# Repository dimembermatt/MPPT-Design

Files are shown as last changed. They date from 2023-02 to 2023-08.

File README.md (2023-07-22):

# :sunny: Sunscatter MPPT-Design - Gen 2 Maximum Power Point Tracker Board

Design and documentation of a custom MPPT for LHR Solar. Created in part with
Professor Alex Hanson's ECE 394J Power Electronics Class.

---

## Repository Structure

- **datasheets** - contains datasheets for major components of the Sunscatter.
- **docs** - contains documentation on how to build, test, and use the Sunscatter.
- **fw** - contains fw that is loaded onto the Sunscatter.
  - **tests** - test programs used to characterize and validate the Sunscatter.
  - **src** - main program used to run the Sunscatter.
  - **inc** - internally developed libraries specific for the Sunscatter.
  - **lib** - third party libraries used by the Sunscatter.
- **hw**
  - **footprints** - project specfic footprint association files for the Sunscatter.
  - **models** - 3d .step files for the PCB 3d viewer.
  - **symbols** - project specific symbol files for the Sunscatter.
  - **vX_Y_Z** - frozen versioning folder for PCB production files.
  - design files
- **sim** - contains a KiCAD project of the bare DC-DC converter of the MPPT, using SPICE parts for simulation.
- **sw** - contains relevant software for operating the automated design pipeline.
  - **design_files**
  - **design_procedures**

---

## Maintainers

The current maintainer of this project is Matthew Yu as of 07/17/2023. His email
is [matthewjkyu@gmail.com](matthewjkyu@gmail.com).

Contributors to the HW and FW encompass many dedicated students, including:

- Jacob Pustilnik
- Pranav Rama
- Sharon Chen

Special thanks to Professor Gary Hallock, who supervised the development and
design of this project.

---

## Versioning

This PCB is on unified version `0.2.0`. Every time the schematic and/or layout
is updated, this version number should go up. We use [semantic
versioning](https://semver.org/) to denote between versions. See the
[changelog](./docs/CHANGELOG.md) for more details.

---

## TODO

### Documentation

### HW

### FW

### SW

### Sim

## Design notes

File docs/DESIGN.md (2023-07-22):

# v0.1.0 DESIGN

TODO: update this consistent with all design versions.
---

## Table of Contents

- [v0.1.0 DESIGN](#v010-design)
  - [TODO: update this consistent with all design versions.](#todo-update-this-consistent-with-all-design-versions)
  - [Table of Contents](#table-of-contents)
  - [Introduction](#introduction)
  - [System Design Requirements](#system-design-requirements)
    - [Input](#input)
    - [Output](#output)
    - [User Specifications](#user-specifications)
  - [Hand Design](#hand-design)
    - [Switch Selection](#switch-selection)
    - [Input and Output Capacitor Selection](#input-and-output-capacitor-selection)
    - [Inductor Selection](#inductor-selection)
      - [Hand Designed Process](#hand-designed-process)
      - [Reverse Engineered Process](#reverse-engineered-process)
    - [Layout](#layout)
    - [Simulation Results](#simulation-results)
    - [Experimental Results](#experimental-results)
  - [Automated Design](#automated-design)
    - [Optimizer Design Output](#optimizer-design-output)
      - [Capacitor FOM](#capacitor-fom)
      - [Inductor Optimization](#inductor-optimization)
    - [Optimizer Simulation Output](#optimizer-simulation-output)
  - [Conclusion and Further Work](#conclusion-and-further-work)

---

## Introduction

This document outlines the design process and results of two comparable MPPT
designs; one that was developed by hand and validated experimentally; the other
generated by our optimization algorithm pipeline.

---

## System Design Requirements

---

### Input

We define the input of the MPPT to be a solar array, consisting of a large
number of photovoltaic cells strung in series with bypass diodes across each
cluster of cells. This solar array, in optimal conditions (STC = $25 \, C$,
$1000 \frac{W}{m^2}$), shall have the following characteristics.

| Property | Value  | Units |
|---|---|---|
| Cell Specific | | |
| $V_{OC}$ | 0.721  | V |
| $I_{SC}$ | 6.15 | A |
| $V_{MPP}$ | 0.621  | V |
| $I_{MPP}$ | 5.84 | A |
| $P_{MPP}$ | 3.63 | W |
| Array Specific | | |
| $N_{CELLS}$ | 111 | |
| $V_{OC}$ | 80.031 | V |
| $I_{SC}$ | 6.15 | A |
| $V_{MPP}$ | 68.931 | V |
| $I_{MPP}$ | 5.84 | A |
| $P_{MPP}$ | 402.56 | W |

A specification of the cell characteristics and the model output used for this
design is shown below.

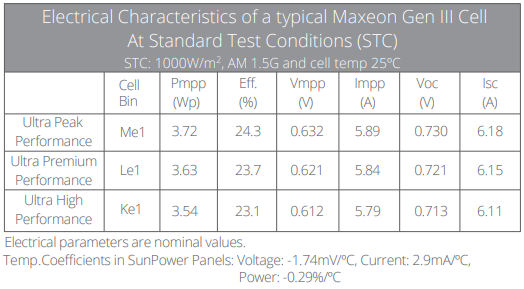
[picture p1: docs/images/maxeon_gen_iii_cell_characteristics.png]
Maxeon Gen III Cell Characteristics

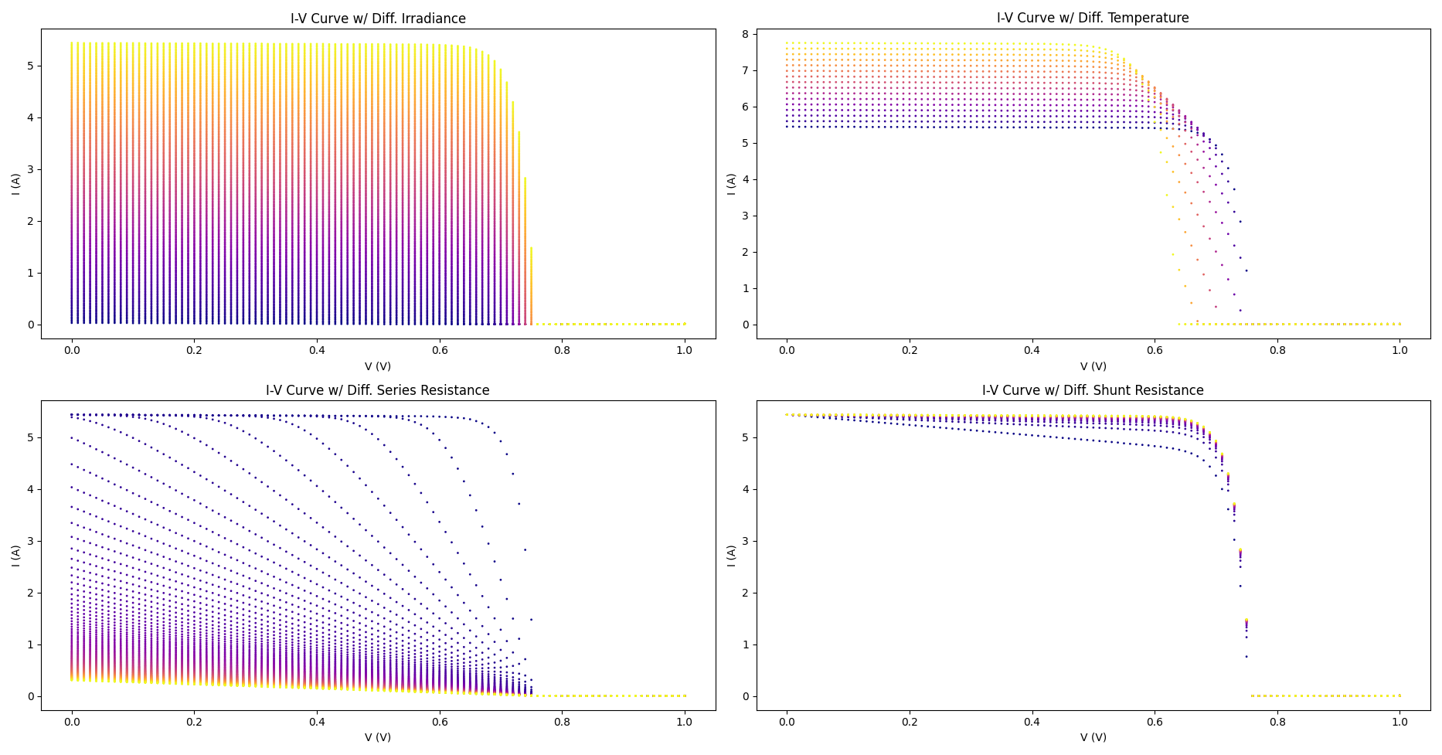
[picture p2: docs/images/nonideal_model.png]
Nonideal Cell Model


---

### Output

We define the output of the MPPT to be a LiMnNi battery pack, with a voltage
range of $V_{BATT} \in [80, 134.4] \, V$. We assume a maximum charging current
of $10 \, A$ at any charge voltage, for lack of a better model.

---

### User Specifications

Using the above input and output, we define the user specifications as follows:

```json
{
    "NAME": "Broad range MPPT",
    "AUTHORS": ["Matthew Yu", "Jacob Pustilnik"],
    "DESCRIPTION": "MPPT Boost Converter v0.1.0",
    "DATE_DESIGNED": "05/07/23",
    "DESIGN": {
        "input_source": {
            "source_model_type": "solar_cell",
            "cell_type": "Maxeon Gen III Bin Le1",
            "num_cells": 111,
            "r_sh": 40,
            "r_s": 0.0035,
            "inp_ripple (V)": 0.725,
            "user_v_range": [20.335, 74.481]
        },
        "output_sink": {
            "sink_model_type": "battery",
            "battery_type": "INR21700-M50LT",
            "num_cells": 32,
            "out_ripple (V)": 1.0,
            "user_v_range": [80, 130]
        },
        "safety_factor": 1.25
    }
}
```

We specify the shunt resistance and series resistance of the solar cell model as
based on empirical data with the I-V Curve Tracer testing setup.

We define the input voltage range to be $V_{ARR} \in [20.335, 74.481] \, V$
during the hand-design process to minimize switch stress and improve system
efficiency.

The input voltage peak-to-peak specification is slightly less than $1 \,\%$ of the
maximum input voltage ($74.481 \, V$).

The output voltage peak-to-peak specification is a conservative estimate of the
requirements of the LHR Solar BPS system. They did not give us a concrete number
(or any number, really), so we surmised that a $1 \, V_{pp}$ ripple should be
sufficient. This also means that for continuous transfer of energy in the
direction of the BPS, the output voltage of the system must be greater than the
voltage of the load plus the half of the ripple. A smaller ripple would allow us
to get closer to the load voltage and can marginally reduce switching stress.

The inductor current peak-to-peak specification is based on the typical $20\,\%$
current ripple ratio used in converters. It was increased to about $22.358\, \%$
due to the optimization process.

We use a safety factor of 1.25 to reduce system risk and improve operational
lifetime.

---

## Hand Design

The first version of this converter, version 0.1.0, was hand designed from
scratch. The following subsections discusses the methodology behind the design,
the expected and actual performance, and ultimately how it informs the automated
design process.

---

### Switch Selection

The main consideration for switch selection is the switching frequency relative
to the power loss; a better switch relative to another will have a higher
switching frequency for the same or less power consumption. Additionally, a
higher switching frequency has knock-on effects for passive selection; it
reduces the effective ripple experienced by the inductors and capacitors and
reduces their energy storage requirements.

One way to quantize switch performance is to use a Figure of Merit (FOM). The
established FOM for MOSFETs is $\tau = R_{DS,ON} * C_{OSS}$; a lower $\tau$
indicates a better switch.

We investigated a set of GaN switches, extracting $R_{DS,ON}$ values at $25 \,C$
and $125 \, C$ and $C_{OSS}$ values at $0 \, V$ and $150 \, V$. Taking the
average of these values, we established the FOM in $ps$.

GaN FETs

To determine the optimal switch, we took the top 12.5 percentile FOM and mapped
the $R_{DS,ON}$ vs $F_{SW,MAX}$ for a given power budget for various operating
points.

FOM Mapping

We see that the worst case plot is when the input voltage is minimized and the
output voltage is maximized. At an $R_{DS,ON}$ of about $19 \, m\Omega$. We
maximize the $F_{SW}$ at around $104 \, kHz$. It can be intuited that
an $R_{DS,ON}$ ratio to $C_{OSS}$ is slightly more important than the overall
FOM value.

As such, the ideal candidate for the design is the EPC2207, which has the
closest $R_{DS,ON}$ at the lowest FOM. This was not available at the time of
design, so the next closest candidate, the EPC2307 was chosen.

Rerunning the calculations of max lower bound $F_{SW}$ for a given power budget,
we achieved a switching frequency of $104 \, kHz$.

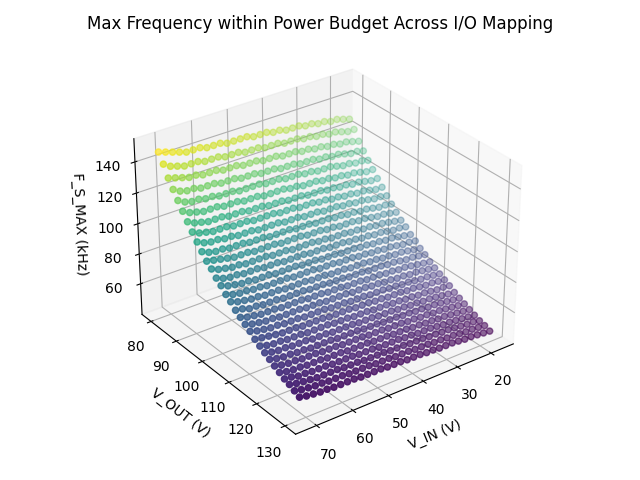
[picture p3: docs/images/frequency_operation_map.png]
$F_{SW}$ Mapping


---

### Input and Output Capacitor Selection

The input and output capacitor selection depends on several parameters:

- the required capacitance needed to reduce ripple to below the design
specification at the worst case operating point,
- the ripple current that needs to be supported by the set of capacitors,
- and the loss due to ESR and leakage current.

The first and second parameters are the constraining function of the capacitor
selection, while the third parameter is the optimization function of the
capacitor selection.

Given the switching frequency of the device, we simulated the minimum
capacitance (and inductance) required to hit the target ripple across the I/O
mapping of the device.

Passive Sizing Mapping

We noted a minimum required input capacitance of $5.5 \, \mu F$ and output capacitance
of $15.2 \, \mu F$ in order to meet or beat our ripple target across the I/O mapping
of the device.

From this, we selected capacitors for bulk capacitance and hf capacitance.
The input capacitor consisted of a single aluminum organic polymer electrolytic
capacitor A759KS156M2AAAE52, with a capacitance of $15 \, \mu F$. The output capacitors
consisted of two aluminum organic polymer electrolytic capacitors
A759MS186M2CAAE90, with a capacitance of $18 \, \mu F$. These bulk capacitances are well
beyond the required capacitance and thus we predict that the expected ripple
will be tighter than required.

We also selected a hf switching node MLCC capacitor to reduce switching noise,
the CGA9P3X7T2E225MA, with a capacitance of $2.2 \, \mu F$. At $125 \, V$ DC bias and
$125 \, C$, the capacitance derating goes down to slightly above $1 \, \mu F$. At
about $100 \, kHz$, the ESR is about $5.5 \, m\Omega$.

---

### Inductor Selection

The inductor selection consists of two components; the inductor core geometry,
and the inductor core material. An ideal inductor is one that minimizes volume
and wire length while keeping losses low.

The minimum inductance calculated by the procedure above was $109.2 \, \mu H$.

It must be noted here that the hand-designed process for calculating the
inductance neglected core gap, which caused issues during the experimental
testing. Below we will present the results of the flawed calculation versus the
reverse engineered variant using the automated design system.

---

#### Hand Designed Process

With a target $110 \, \mu H$ inductance, the hand-designed process generated a
design using the EPCOS/TDK PQ26/25, 3C97 core, the B65877A0000R097. It required
35 turns with a wire gauge of 21 AWG.

This results in a estimated conduction loss of $4.5 \, W$ and core loss of
$0.2 \, W$.

---

#### Reverse Engineered Process

Using the same core, the algorithm determined that the inductor requires 31
turns of 19 AWG wire with a core gap of $1.0 \, mm$ per side of the core.

This results in an estimated conduction loss of $0.3 \, W$ and a core loss of
$0.03 \, W$.

As can be seen, the reverse engineered process results in a much lower
conduction and core loss. Part of the changes between the two designs is that it
was determined experimentally that the 0.3 winding factor used for calculating
the number of turns that can fit around the core was an overly-conservative
estimate, this has been increased to 0.5. In tern, this allows for fitting a
thicker gauge wire which can significantly reduce conduction loss, which appears
to be the main mode of inductor loss during experimental testing.

---

### Layout

This layout section discusses component placement in brief; it does not discuss
in detail all PCB design decisions. Matthew could give an hour lecture if you
ask him to :).

Not discussed in document in detail is the gate driver and PWM generator; the
TI LMG1210RVRR gate driver was chosen for our particular GaN FETs, and the
STM32L432KC is a $80 \, MHz$ microcontroller with PWM outputs. The MCU is paired
with two voltage and current sensors at the ends of the power path for
measurement and closed loop control.

The digital and analog control and measurement circuitry is isolated on the
"top" half of the board layout; this is to prevent or reduce EMI from the
switching node and high current fluctuations.

The "bottom" half of the board layout is the power path; this is the DC-DC
converter and contains the capacitors, inductor, and switches. Components are
arranged relatively linearly to reduce the loop and shape complexity; the bulk
output capacitors can be slightly away from the switching loop but the HF
capacitor must be as close to the switches as possible. Likewise, the inductor
end must also be relatively close to the switches.

In our configuration, we put the switches side by side with the HF MLCC
capacitor directly underneath; this gives a very tight loop.

We also placed thermal jumpers between planes to help distribute heat. This is
accompanied by thermal and EMI stiching vias scattered across the board.

Layout
Assembly

---

### Simulation Results

The following graphs are generated from the automated design system with the
chosen devices provided as parameters.

Source Model

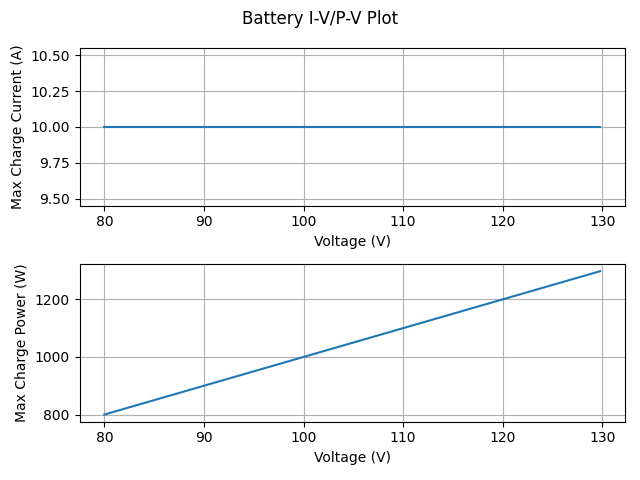
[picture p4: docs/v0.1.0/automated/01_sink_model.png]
Sink Model


Duty Cycle Map

Current Transfer Map

Power Transfer Map

Switch Losses Map

Switch Thermal Sizing

Switch Deadtime Sizing

Passive Ripple Map

Passive Losses Map

Efficiency Map

We note that the total power loss derived from the hand-picked design is
$7.63 \, W$, at the highest switching stress operating point: min input voltage,
max output voltage. This results in a minimum transfer efficiency of $93.92 \, \%$.

At this operating point the switch conduction loss and switching loss peaks,
contributing to about $3.60 \, W$ of loss each, with the inductor and output
capacitor providing the majority of the rest (generally through output capacitor
leakage loss and inductor conduction loss).

We also note that minimum required area needed to maintain both switches below
the maximum rated temperature time the 1 / safety factor starting from $60 \, C$ is
$70.893 \, cm^2$. The layout design has a total surface area of $110 \, cm^2$,
which is should be sufficient for cooling without an external heatsink.

---

### Experimental Results

Note for the purposes of the experimental testing, we ran the device at
$100 \, kHz$.

We also used an inductor wound at $155 \, \mu H$, with about 30 turns of AWG 21
wires, and a gap on each side of the core of roughly $0.318 \, mm$.

We obtained the following experimental results:

| Vin (V) | Vout (V) | Pout (W) | Eff (%) | Pdensity (W/cm3) | Vin, p-p (V) | Vout, p-p (V) | Il, p-p (A) |
|---|---|---|---|---|---|---|---|
| 67.524 (69) | 102.02 (105) | 380.87 (400) |  98.972 | 1.979 | 0.234 | 0.309 | 1.820 |
| Broad range tests | | | | | | | |
| 18.752 | 73.242 | 83.154 |  97.349 | 0.432 | 0.226 | 0.365 | 1.159 |
| 18.825 | 96.73 | 84.416 |  97.032 | 0.439 | 0.249 | 0.402 | 1.263 |
| 18.823 | 119.35 | 83.889 |  96.531 | 0.436 | 0.330 | 0.510 | 1.440 |
| 38.805 | 76.688 | 181.72 |  98.616 | 0.944 | 0.270 | 0.356 | 1.520 |
| 38.782 | 100.8 | 182.74 |  98.348 | 0.949 | 0.295 | 0.412 | 1.959 |
| 38.78 | 124.54 | 182.34 |  98.083 | 0.947 | 0.336 | 0.489 | 2.199 |
| 58.798 | 77.774 | 279.2 |  99.103 | 1.450 | 0.249 | 0.348 | 1.280 |
| 58.76 | 102.01 | 281.43 |  98.904 | 1.462 | 0.299 | 0.411 | 2.000 |
| 58.741 | 126.28 | 282.55 |  98.671 | 1.468 | 0.346 | 0.495 | 2.480 |
| 67.592 | 77.744 | 371.13 |  99.146 | 1.928 | 0.149 | 0.278 | 0.840 |
| 67.524 | 102.02 | 380.87 |  98.972 | 1.979 | 0.234 | 0.309 | 1.820 |
| 67.471 | 126.19 | 375.78 |  98.782 | 1.952 | 0.265 | 0.325 | 2.540 |
| 74.612 | 79.447 | 97.746 |  99.071 | 0.508 | 0.217 | 0.428 | 0.580 |
| 74.609 | 104.35 | 98.194 |  98.484 | 0.510 | 0.226 | 0.419 | 1.640 |
| 74.606 | 129.25 | 98.805 |  97.806 | 0.513 | 0.273 | 0.457 | 2.359 |

We note that the switching noise was minimal, indicating that the switching node
layout was optimized well enough to not severely impact the design results.

We measured a worst I/O mapping efficiency ($18.8 \, V$ to $119.3 \, V$) of
$96.5 \, \%$, exceeding our expected lower bound. We measured a best I/O mapping
efficiency ($67.6 \, V$ to $77.7 \, V$) of $99.1 \, \%$, within measurement error
to meet our upper bound.

We do not meet our simulated ripple results, potentially due the following
factors, but still comfortably beat our ripple specifications by up to 50%.

- measurement error (using oscilloscope)
- switching noise
- change in inductor design

We observe that the experimental data power loss map shows deviations from
simulation; if we observe the trend of loss increase across each axis, the
underlying switching and conduction loss agree. In between however, some
datapoints exceed expectations and have larger losses than can be explained by
simulations (although some may be attributable to inductor loss at the input
MPP).

Power Loss Map

Efficiency Map

Thermal wise, the losses were expected to be in two main components: the
switches and inductor. According to the thermal images, this shows up as
expected. The maximum recorded temperature of the switch devices was $60 \, C$,
from am ambient of about $20 \, C$, the 40 degree temperature increase is in
line with the anticipated loss at that particular operating point (~$3.6 \, W$).

Thermal Images

---

## Automated Design

Optimizer Block Diagram

An automated design optimizer algorithm was developed to speed up and improve
the design process outlined by the hand designed procedures.

A design specification file and a list of design components are provided, in
which the optimizer chooses the optimal parts and calculates the operating
parameters that maximizes system efficiency.

Optimizer Parameters and Constraints

The optimizer controls two parameters: the power budget allocated to each switch
and the inductor current ripple ratio. The user maintains constraints, including
the input voltage and output voltage range, or the safety factor of the design.

Optimizer Algorithm

As outlined in the optimizer algorithm, every design iteration starts with a
selection on the switch power budget and the inductor current ripple ratio. The
algorithm first determines the switch and the switching frequency before
selecting for an optimal set of capacitors and then the inductor configuration.
Finally, the overall worst case power loss is determined before repeating the
loop.

After many iterations, the optimizer settles on the parameters that lead to the
highest efficiency design. The output of these parameters results in the
selection of design components for use.

The automated design was ran on the same specification file and user constraints
as defined in the hand-designed section.

---

### Optimizer Design Output

It was evaluated that the optimal parameter values that led to the ideal design
was an $R_{L}$ of 0.119 and a $P_{SW\_BUD}$ of 2.13 W.

The switches chosen were the EPC2207 (now in stock), which had an optimal
frequency of $95 \, kHz$; this led to the following passive requirements:

- Input capacitance greater than $2.67 \, \mu F$
- Output capacitance greater than $16.16 \, \mu F$
- Inductance greater than $280.51 \, \mu H$.

---

#### Capacitor FOM

A custom FOM was developed for selecting optimal capacitors for the design. We
remind the reader of the parameters defined earlier in the hand-design section
for choosing capacitors:

> - the required capacitance needed to reduce ripple to below the design
>   specification at the worst case operating point,
> - the ripple current that needs to be supported by the set of capacitors,
> - and the loss due to ESR and leakage current.
>
> The first and second parameters are the constraining function of the capacitor
> selection, while the third parameter is the optimization function of the
> capacitor selection.

Ideally, we want to choose as few capacitors as possible to meet the first two
parameters, but also minimize the third parameter. As this is a multi-objective
optimization problem, the brute force method would be to form the power set of
all candidate capacitors, filter the sets that do not meet the constraints, and
choose the smallest and most optimal set.

However, we propose the following FOM equation to speed up the process:

$$
FOM = \frac{V_{D} * C * I_{RIPPLE}}{ESR * I_{LEAKAGE} * COST}
$$

As can be seen, this formula rewards higher constraints while punishing
undesirable aspects that affect power (and cost).

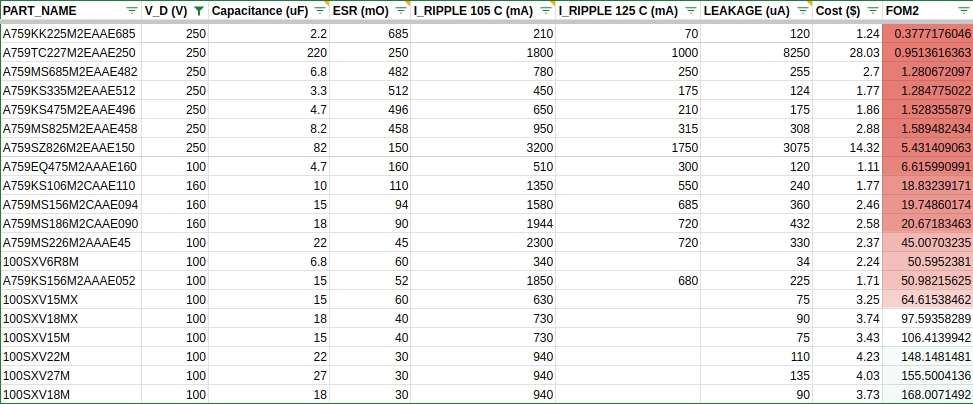
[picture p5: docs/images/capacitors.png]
Capacitors


A subset of capacitors with the FOM added is shown. We can see that the best FOM
capacitors tended to have reasonable capacitance, ripple, and cost, but low ESR,
and leakage.

Ultimately this worked well for this design, with the optimizer choosing the
HZA336M080G24T-F $33 \, \mu F$ aluminium electrolytic capacitor for the input
and the A759MS186M2CAAE090 $18 \, \mu F$ aluminum organic polymer electrolytic
capacitor for the output.

---

#### Inductor Optimization

The optimizer selected a slightly different core than the hand-design, a
PQ26/25-3C96 with 53 turns of 21 AWG wire. A core gap of 1.4 mm is suggested.

Inductor selection was performed with extra component listings for the core
shape and material: the material in particular provided constants calculated by
FerroxCube to calculate the core loss with Steinmetz' equation. This meant that
there was no need to manually infer the $P_{V}$ from the manufacturer datasheet
for our particular frequency, core shape, and temperature.

The optimization procedure only optimizes for loss, however; other parameters of
interest, like cost and core size are neglected in favor of the design with the
least conduction and core loss.

---

### Optimizer Simulation Output

The following graphs are generated from the automated design system with the
chosen devices provided as parameters.

Source Model

Sink Model

Duty Cycle Map

Current Transfer Map

Power Transfer Map

Switch Losses Map

Switch Thermal Sizing

Switch Deadtime Sizing

Passive Ripple Map

Passive Losses Map

Efficiency Map

We note that the total power loss derived from the automated design is
$5.04 \, W$, at the highest switching stress operating point: min input voltage,
max output voltage. This results in a minimum transfer efficiency of $96.0 \, \%$.

At this operating point the switch conduction loss and switching loss peaks,
contributing to about $2.12 \, W$ of loss each, with the inductor conduction
loss providing the rest.

We also note that minimum required area needed to maintain both switches below
the maximum rated temperature time the 1 / safety factor starting from $60 \, C$ is
$35.546 \, cm^2$, a 2x improvement. This allows us to shrink the required
exposed thermal area by a significant margin, and should enable us to remove the
existing thermal jumpers.

Also notably improved is the dead time, with the majority of the design only
needing at most $12 ns$ of deadtime.

We see that this automated design beats the reverse engineered hand-designed
version by at least $2 \, \%$. The upper bound efficiency also improves
marginally. At the same time, our expected number of capacitors decreases, our
required thermal area shrinks, and thus we can remove extraneous components like
heat sinks, and thermal jumpers.

Judging by our empirical losses, it would be very positive if we can exceed our
lower bound efficiency estimate again.

---

## Conclusion and Further Work

In conclusion, the overall system design is a good starting point towards
modeling DC-DC converters with only a few known parameters. A hand-designed
system is compared against a fully automated result, and the initial efficiency
results, both simulated and emperical, show high marks. The automated design
appears to improve upon the hand-designed converter by at least $2 \, \%$ in the
worst operating regime, which is promising.

In this report, we do not discuss the open and closed loop stability of the
design. However, we have validated that the system is indeed open and closed
loop stable. Further work in this project will involve the small signal and
large signal stability analysis of the system to characterize the stability of
the system before comparing it against empirical stability.

In addition to this analysis, further effort should be performed to gather higher
resolution steady state efficiency. More experimental data points can help
inform the accuracy of the model and where the design process can be improved.

Further research into choosing an appropriate FOM should be performed.
While the proposed FOM works well for this design, it is likely not optimal in
all cases: a brute force solution should be determined as the golden reference,
and a PCA or curve fitting technique should be performed on the available
capacitor parameters to determine weightings for the values that match the golden
reference.

Finally, work into automating the decision of choosing HF capacitors should be
performed. This is slightly more difficult for MLCCs due to the data-intensive
work of gathering frequency vs impedance CSVs (and so forth) from manufacturers
that provide them, such as KEMET and TDK. However, their data can improve the
optimization process and provide useful insight into stability analysis due to
their effects on the design poles and holes.

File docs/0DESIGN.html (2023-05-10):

# v0.1.0 DESIGN

## Table of Contents

- v0.1.0 DESIGN
  - Table of Contents
  - Introduction
  - System Design Requirements
    - Input
    - Output
    - User Specifications
  - Hand Design
    - Switch Selection
    - Input and Output Capacitor Selection
    - Inductor Selection
      - Hand Designed Process
      - Reverse Engineered Process
    - Layout
    - Simulation Results
    - Experimental Results
  - Automated Design
    - Optimizer Design Output
      - Capacitor FOM
      - Inductor Optimization
    - Optimizer Simulation Output
  - Conclusion and Further Work

## Introduction

This document outlines the design process and results of two comparable MPPT designs; one that was developed by hand and validated experimentally; the other generated by our optimization algorithm pipeline.

## System Design Requirements

### Input

We define the input of the MPPT to be a solar array, consisting of a large number of photovoltaic cells strung in series with bypass diodes across each cluster of cells. This solar array, in optimal conditions (STC = 25 \, C, 1000 \frac{W}{m^2}), shall have the following characteristics.

Property | Value | Units
Cell Specific
V_{OC} | 0.721 | V
I_{SC} | 6.15 | A
V_{MPP} | 0.621 | V
I_{MPP} | 5.84 | A
P_{MPP} | 3.63 | W
Array Specific
N_{CELLS} | 111
V_{OC} | 80.031 | V
I_{SC} | 6.15 | A
V_{MPP} | 68.931 | V
I_{MPP} | 5.84 | A
P_{MPP} | 402.56 | W

A specification of the cell characteristics and the model output used for this design is shown below.

Maxeon Gen III Cell Characteristics Nonideal Cell Model

### Output

We define the output of the MPPT to be a LiMnNi battery pack, with a voltage range of V_{BATT} \in [80, 134.4] \, V. We assume a maximum charging current of 10 \, A at any charge voltage, for lack of a better model.

### User Specifications

Using the above input and output, we define the user specifications as follows:

{
    "NAME": "Broad range MPPT",
    "AUTHORS": ["Matthew Yu", "Jacob Pustilnik"],
    "DESCRIPTION": "MPPT Boost Converter v0.1.0",
    "DATE_DESIGNED": "05/07/23",
    "DESIGN": {
        "input_source": {
            "source_model_type": "solar_cell",
            "cell_type": "Maxeon Gen III Bin Le1",
            "num_cells": 111,
            "r_sh": 40,
            "r_s": 0.0035,
            "inp_ripple (V)": 0.725,
            "user_v_range": [20.335, 74.481]
        },
        "output_sink": {
            "sink_model_type": "battery",
            "battery_type": "INR21700-M50LT",
            "num_cells": 32,
            "out_ripple (V)": 1.0,
            "user_v_range": [80, 130]
        },
        "safety_factor": 1.25
    }
}

We specify the shunt resistance and series resistance of the solar cell model as based on empirical data with the I-V Curve Tracer testing setup.

We define the input voltage range to be V_{ARR} \in [20.335, 74.481] \, V during the hand-design process to minimize switch stress and improve system efficiency.

The input voltage peak-to-peak specification is slightly less than 1 \,\% of the maximum input voltage (74.481 \, V).

The output voltage peak-to-peak specification is a conservative estimate of the requirements of the LHR Solar BPS system. They did not give us a concrete number (or any number, really), so we surmised that a 1 \, V_{pp} ripple should be sufficient. This also means that for continuous transfer of energy in the direction of the BPS, the output voltage of the system must be greater than the voltage of the load plus the half of the ripple. A smaller ripple would allow us to get closer to the load voltage and can marginally reduce switching stress.

The inductor current peak-to-peak specification is based on the typical 20\,\% current ripple ratio used in converters. It was increased to about 22.358\, \% due to the optimization process.

We use a safety factor of 1.25 to reduce system risk and improve operational lifetime.

## Hand Design

The first version of this converter, version 0.1.0, was hand designed from scratch. The following subsections discusses the methodology behind the design, the expected and actual performance, and ultimately how it informs the automated design process.

### Switch Selection

The main consideration for switch selection is the switching frequency relative to the power loss; a better switch relative to another will have a higher switching frequency for the same or less power consumption. Additionally, a higher switching frequency has knock-on effects for passive selection; it reduces the effective ripple experienced by the inductors and capacitors and reduces their energy storage requirements.

One way to quantize switch performance is to use a Figure of Merit (FOM). The established FOM for MOSFETs is \tau = R_{DS,ON} * C_{OSS}; a lower \tau indicates a better switch.

We investigated a set of GaN switches, extracting R_{DS,ON} values at 25 \,C and 125 \, C and C_{OSS} values at 0 \, V and 150 \, V. Taking the average of these values, we established the FOM in ps.

GaN FETs

To determine the optimal switch, we took the top 12.5 percentile FOM and mapped the R_{DS,ON} vs F_{SW,MAX} for a given power budget for various operating points.

FOM Mapping

We see that the worst case plot is when the input voltage is minimized and the output voltage is maximized. At an R_{DS,ON} of about 19 \, m\Omega. We maximize the F_{SW} at around 104 \, kHz. It can be intuited that an R_{DS,ON} ratio to C_{OSS} is slightly more important than the overall FOM value.

As such, the ideal candidate for the design is the EPC2207, which has the closest R_{DS,ON} at the lowest FOM. This was not available at the time of design, so the next closest candidate, the EPC2307 was chosen.

Rerunning the calculations of max lower bound F_{SW} for a given power budget, we achieved a switching frequency of 104 \, kHz.

Mapping

### Input and Output Capacitor Selection

The input and output capacitor selection depends on several parameters:

- the required capacitance needed to reduce ripple to below the design specification at the worst case operating point,
- the ripple current that needs to be supported by the set of capacitors,
- and the loss due to ESR and leakage current.

The first and second parameters are the constraining function of the capacitor selection, while the third parameter is the optimization function of the capacitor selection.

Given the switching frequency of the device, we simulated the minimum capacitance (and inductance) required to hit the target ripple across the I/O mapping of the device.

Passive Sizing Mapping

We noted a minimum required input capacitance of 5.5 \, \mu F and output capacitance of 15.2 \, \mu F in order to meet or beat our ripple target across the I/O mapping of the device.

From this, we selected capacitors for bulk capacitance and hf capacitance. The input capacitor consisted of a single aluminum organic polymer electrolytic capacitor A759KS156M2AAAE52, with a capacitance of 15 \, \mu F. The output capacitors consisted of two aluminum organic polymer electrolytic capacitors A759MS186M2CAAE90, with a capacitance of 18 \, \mu F. These bulk capacitances are well beyond the required capacitance and thus we predict that the expected ripple will be tighter than required.

We also selected a hf switching node MLCC capacitor to reduce switching noise, the CGA9P3X7T2E225MA, with a capacitance of 2.2 \, \mu F. At 125 \, V DC bias and 125 \, C, the capacitance derating goes down to slightly above 1 \, \mu F. At about 100 \, kHz, the ESR is about 5.5 \, m\Omega.

### Inductor Selection

The inductor selection consists of two components; the inductor core geometry, and the inductor core material. An ideal inductor is one that minimizes volume and wire length while keeping losses low.

The minimum inductance calculated by the procedure above was 109.2 \, \mu H.

It must be noted here that the hand-designed process for calculating the inductance neglected core gap, which caused issues during the experimental testing. Below we will present the results of the flawed calculation versus the reverse engineered variant using the automated design system.

#### Hand Designed Process

With a target 110 \, \mu H inductance, the hand-designed process generated a design using the EPCOS/TDK PQ26/25, 3C97 core, the B65877A0000R097. It required 35 turns with a wire gauge of 21 AWG.

This results in a estimated conduction loss of 4.5 \, W and core loss of 0.2 \, W.

#### Reverse Engineered Process

Using the same core, the algorithm determined that the inductor requires 31 turns of 19 AWG wire with a core gap of 1.0 \, mm per side of the core.

This results in an estimated conduction loss of 0.3 \, W and a core loss of 0.03 \, W.

As can be seen, the reverse engineered process results in a much lower conduction and core loss. Part of the changes between the two designs is that it was determined experimentally that the 0.3 winding factor used for calculating the number of turns that can fit around the core was an overly-conservative estimate, this has been increased to 0.5. In tern, this allows for fitting a thicker gauge wire which can significantly reduce conduction loss, which appears to be the main mode of inductor loss during experimental testing.

### Layout

This layout section discusses component placement in brief; it does not discuss in detail all PCB design decisions. Matthew could give an hour lecture if you ask him to :).

Not discussed in document in detail is the gate driver and PWM generator; the TI LMG1210RVRR gate driver was chosen for our particular GaN FETs, and the STM32L432KC is a 80 \, MHz microcontroller with PWM outputs. The MCU is paired with two voltage and current sensors at the ends of the power path for measurement and closed loop control.

The digital and analog control and measurement circuitry is isolated on the "top" half of the board layout; this is to prevent or reduce EMI from the switching node and high current fluctuations.

The "bottom" half of the board layout is the power path; this is the DC-DC converter and contains the capacitors, inductor, and switches. Components are arranged relatively linearly to reduce the loop and shape complexity; the bulk output capacitors can be slightly away from the switching loop but the HF capacitor must be as close to the switches as possible. Likewise, the inductor end must also be relatively close to the switches.

In our configuration, we put the switches side by side with the HF MLCC capacitor directly underneath; this gives a very tight loop.

We also placed thermal jumpers between planes to help distribute heat. This is accompanied by thermal and EMI stiching vias scattered across the board.

Layout Assembly

### Simulation Results

The following graphs are generated from the automated design system with the chosen devices provided as parameters.

Source Model

Sink Model

Duty Cycle Map

Current Transfer Map

Power Transfer Map

Switch Losses Map

Switch Thermal Sizing

Switch Deadtime Sizing

Passive Ripple Map

Passive Losses Map

Efficiency Map

We note that the total power loss derived from the hand-picked design is 7.63 \, W, at the highest switching stress operating point: min input voltage, max output voltage. This results in a minimum transfer efficiency of 93.92 \, \%.

At this operating point the switch conduction loss and switching loss peaks, contributing to about 3.60 \, W of loss each, with the inductor and output capacitor providing the majority of the rest (generally through output capacitor leakage loss and inductor conduction loss).

We also note that minimum required area needed to maintain both switches below the maximum rated temperature time the 1 / safety factor starting from 60 \, C is 70.893 \, cm^2. The layout design has a total surface area of 110 \, cm^2, which is should be sufficient for cooling without an external heatsink.

### Experimental Results

Note for the purposes of the experimental testing, we ran the device at 100 \, kHz.

We also used an inductor wound at 155 \, \mu H, with about 30 turns of AWG 21 wires, and a gap on each side of the core of roughly 0.318 \, mm.

We obtained the following experimental results:

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

We note that the switching noise was minimal, indicating that the switching node layout was optimized well enough to not severely impact the design results.

We measured a worst I/O mapping efficiency (18.8 \, V to 119.3 \, V) of 96.5 \, \%, exceeding our expected lower bound. We measured a best I/O mapping efficiency (67.6 \, V to 77.7 \, V) of 99.1 \, \%, within measurement error to meet our upper bound.

We do not meet our simulated ripple results, potentially due the following factors, but still comfortably beat our ripple specifications by up to 50%.

- measurement error (using oscilloscope)
- switching noise
- change in inductor design

We observe that the experimental data power loss map shows deviations from simulation; if we observe the trend of loss increase across each axis, the underlying switching and conduction loss agree. In between however, some datapoints exceed expectations and have larger losses than can be explained by simulations (although some may be attributable to inductor loss at the input MPP).

Power Loss Map

Efficiency Map

Thermal wise, the losses were expected to be in two main components: the switches and inductor. According to the thermal images, this shows up as expected. The maximum recorded temperature of the switch devices was 60 \, C, from am ambient of about 20 \, C, the 40 degree temperature increase is in line with the anticipated loss at that particular operating point (~3.6 \, W).

Thermal Images

## Automated Design

Optimizer Block Diagram

An automated design optimizer algorithm was developed to speed up and improve the design process outlined by the hand designed procedures.

A design specification file and a list of design components are provided, in which the optimizer chooses the optimal parts and calculates the operating parameters that maximizes system efficiency.

Optimizer Parameters and Constraints

The optimizer controls two parameters: the power budget allocated to each switch and the inductor current ripple ratio. The user maintains constraints, including the input voltage and output voltage range, or the safety factor of the design.

Optimizer Algorithm

As outlined in the optimizer algorithm, every design iteration starts with a selection on the switch power budget and the inductor current ripple ratio. The algorithm first determines the switch and the switching frequency before selecting for an optimal set of capacitors and then the inductor configuration. Finally, the overall worst case power loss is determined before repeating the loop.

After many iterations, the optimizer settles on the parameters that lead to the highest efficiency design. The output of these parameters results in the selection of design components for use.

The automated design was ran on the same specification file and user constraints as defined in the hand-designed section.

### Optimizer Design Output

It was evaluated that the optimal parameter values that led to the ideal design was an R_{L} of 0.119 and a P_{SW\_BUD} of 2.13 W.

The switches chosen were the EPC2207 (now in stock), which had an optimal frequency of 95 \, kHz; this led to the following passive requirements:

- Input capacitance greater than 2.67 \, \mu F
- Output capacitance greater than 16.16 \, \mu F
- Inductance greater than 280.51 \, \mu H.

#### Capacitor FOM

A custom FOM was developed for selecting optimal capacitors for the design. We remind the reader of the parameters defined earlier in the hand-design section for choosing capacitors:

- the required capacitance needed to reduce ripple to below the design specification at the worst case operating point,
- the ripple current that needs to be supported by the set of capacitors,
- and the loss due to ESR and leakage current.

The first and second parameters are the constraining function of the capacitor selection, while the third parameter is the optimization function of the capacitor selection.

Ideally, we want to choose as few capacitors as possible to meet the first two parameters, but also minimize the third parameter. As this is a multi-objective optimization problem, the brute force method would be to form the power set of all candidate capacitors, filter the sets that do not meet the constraints, and choose the smallest and most optimal set.

However, we propose the following FOM equation to speed up the process:

FOM = \frac{V_{D} * C * I_{RIPPLE}}{ESR * I_{LEAKAGE} * COST}

As can be seen, this formula rewards higher constraints while punishing undesirable aspects that affect power (and cost).

Capacitors

A subset of capacitors with the FOM added is shown. We can see that the best FOM capacitors tended to have reasonable capacitance, ripple, and cost, but low ESR, and leakage.

Ultimately this worked well for this design, with the optimizer choosing the HZA336M080G24T-F 33 \, \mu F aluminium electrolytic capacitor for the input and the A759MS186M2CAAE090 18 \, \mu F aluminum organic polymer electrolytic capacitor for the output.

#### Inductor Optimization

The optimizer selected a slightly different core than the hand-design, a PQ26/25-3C96 with 53 turns of 21 AWG wire. A core gap of 1.4 mm is suggested.

Inductor selection was performed with extra component listings for the core shape and material: the material in particular provided constants calculated by FerroxCube to calculate the core loss with Steinmetz' equation. This meant that there was no need to manually infer the P_{V} from the manufacturer datasheet for our particular frequency, core shape, and temperature.

The optimization procedure only optimizes for loss, however; other parameters of interest, like cost and core size are neglected in favor of the design with the least conduction and core loss.

### Optimizer Simulation Output

The following graphs are generated from the automated design system with the chosen devices provided as parameters.

Source Model

Sink Model

Duty Cycle Map

Current Transfer Map

Power Transfer Map

Switch Losses Map

Switch Thermal Sizing

Switch Deadtime Sizing

Passive Ripple Map

Passive Losses Map

Efficiency Map

We note that the total power loss derived from the automated design is 5.04 \, W, at the highest switching stress operating point: min input voltage, max output voltage. This results in a minimum transfer efficiency of 96.0 \, \%.

At this operating point the switch conduction loss and switching loss peaks, contributing to about 2.12 \, W of loss each, with the inductor conduction loss providing the rest.

We also note that minimum required area needed to maintain both switches below the maximum rated temperature time the 1 / safety factor starting from 60 \, C is 35.546 \, cm^2, a 2x improvement. This allows us to shrink the required exposed thermal area by a significant margin, and should enable us to remove the existing thermal jumpers.

Also notably improved is the dead time, with the majority of the design only needing at most 12 ns of deadtime.

We see that this automated design beats the reverse engineered hand-designed version by at least 2 \, \%. The upper bound efficiency also improves marginally. At the same time, our expected number of capacitors decreases, our required thermal area shrinks, and thus we can remove extraneous components like heat sinks, and thermal jumpers.

Judging by our empirical losses, it would be very positive if we can exceed our lower bound efficiency estimate again.

## Conclusion and Further Work

In conclusion, the overall system design is a good starting point towards modeling DC-DC converters with only a few known parameters. A hand-designed system is compared against a fully automated result, and the initial efficiency results, both simulated and emperical, show high marks. The automated design appears to improve upon the hand-designed converter by at least 2 \, \% in the worst operating regime, which is promising.

In this report, we do not discuss the open and closed loop stability of the design. However, we have validated that the system is indeed open and closed loop stable. Further work in this project will involve the small signal and large signal stability analysis of the system to characterize the stability of the system before comparing it against empirical stability.

In addition to this analysis, further effort should be performed to gather higher resolution steady state efficiency. More experimental data points can help inform the accuracy of the model and where the design process can be improved.

Further research into choosing an appropriate FOM should be performed. While the proposed FOM works well for this design, it is likely not optimal in all cases: a brute force solution should be determined as the golden reference, and a PCA or curve fitting technique should be performed on the available capacitor parameters to determine weightings for the values that match the golden reference.

Finally, work into automating the decision of choosing HF capacitors should be performed. This is slightly more difficult for MLCCs due to the data-intensive work of gathering frequency vs impedance CSVs (and so forth) from manufacturers that provide them, such as KEMET and TDK. However, their data can improve the optimization process and provide useful insight into stability analysis due to their effects on the design poles and holes.

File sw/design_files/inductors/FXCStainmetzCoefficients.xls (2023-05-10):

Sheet: Loss Coefficients
 |  |  |  |  |  |  |  |  |  | Freq |  |  | 200000 | Hz | (Sine signal)
 |  |  |  |  |  |  |  |  |  | B |  |  | 0.15 | T
 |  |  |  |  | (f in Hz, B in T, T in deg C) |  |  |  |  | T |  |  | 100 | C
(see not in the bottom)
Material | Status | Freq min | Freq max | Cm | x_1 | y_1 | Ct2_1 | Ct1_1 | Ct_1 | Freq chk |  |  | Pv (mw/cc) |  | Update | T [C] | 20 | 40 | 60 | 80 | 100 | 120 | B [T] | 0.005 | 0.01 | 0.02 | 0.05 | 0.1 | 0.15 | 0.2 | 0.25 | 0.3 | 0.35
3C90 | Standard | 20000 | 200001 | 3.2 | 1.46 | 2.75 | 0.000165 | 0.031 | 2.45 | 1 | 1 | 2 | 952.59 |  |  | 3C90 F=200 B=150 | 1806.105301 | 1404.11351 | 1127.863226 | 977.3544511 | 952.5871843 | 1053.561426 | 3C90 F=200 T=100C | 0.08256980975 | 0.5554612562 | 3.736683033 | 46.43241623 | 312.3588189 | 952.5871843
3C91 | Standard | 10000 | 100000 | 3.5 | 1.4 | 2.5 | 0.000142 | 0.013 | 0.88 | 1 | 0 | 1
3C91 |  | 100000 | 200000 | 3.5 | 1.4 | 2.5 | 0.000142 | 0.013 | 0.88 | 1 | 0 | 1
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

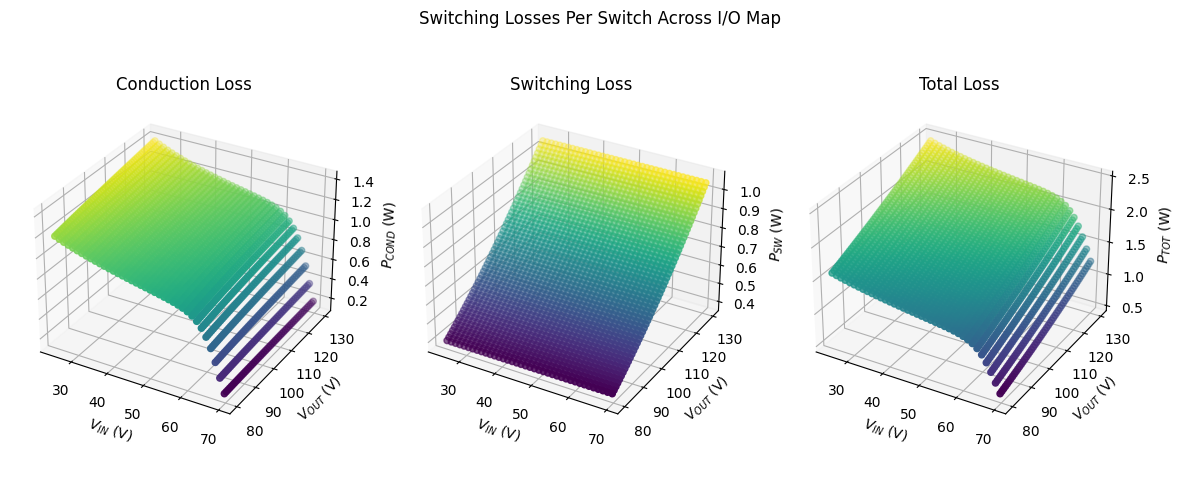
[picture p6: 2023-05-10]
docs/v0.3.0/automated/05_sw_losses_map.png

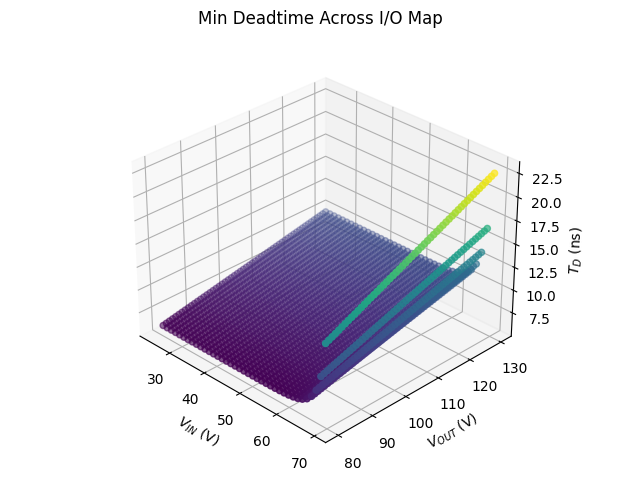
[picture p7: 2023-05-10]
docs/v0.3.0/automated/07_sw_deadtime_map.png

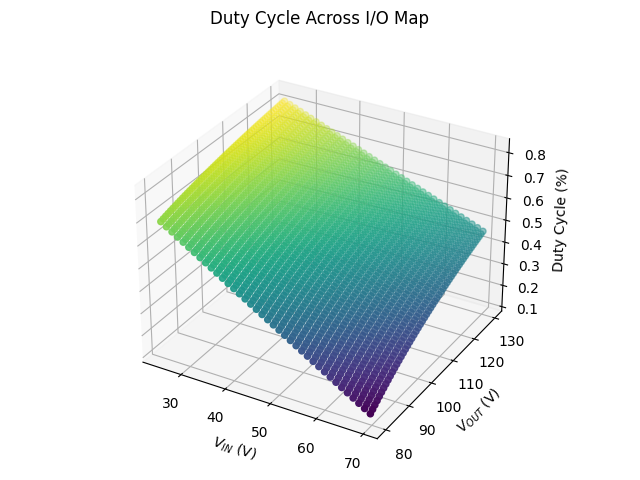
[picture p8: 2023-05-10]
docs/v0.3.0/automated/02_duty_cycle_map.png

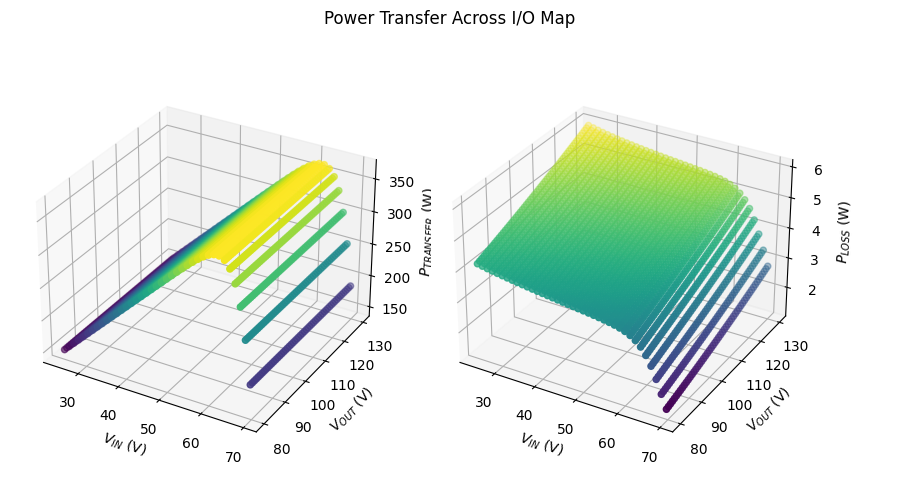
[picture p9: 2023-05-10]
docs/v0.3.0/automated/04_power_map.png

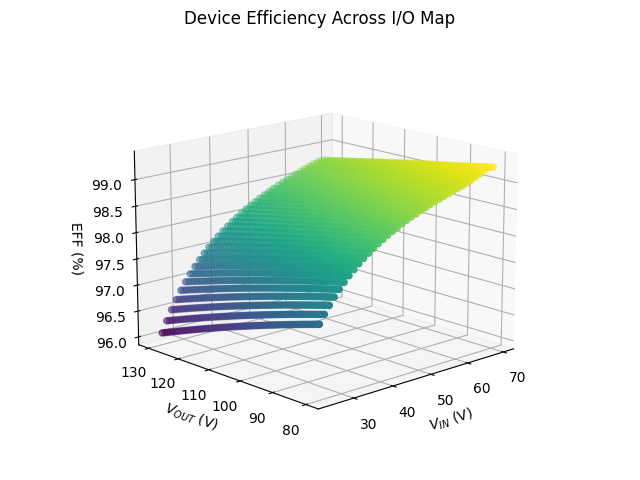
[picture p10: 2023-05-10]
docs/v0.3.0/automated/10_efficiency_map.png

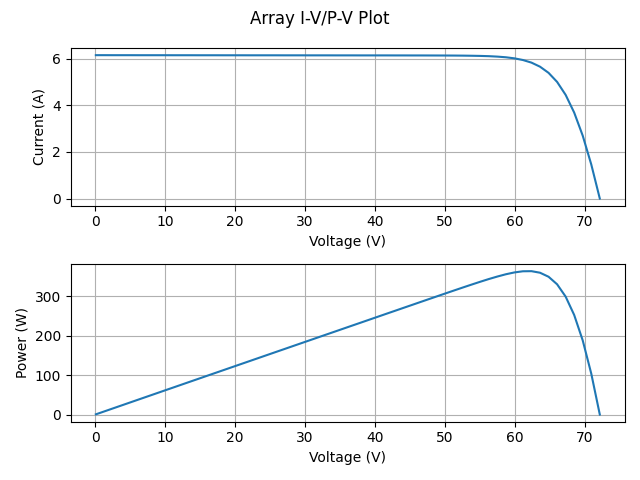
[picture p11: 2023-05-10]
docs/v0.3.0/automated/00_source_model.png

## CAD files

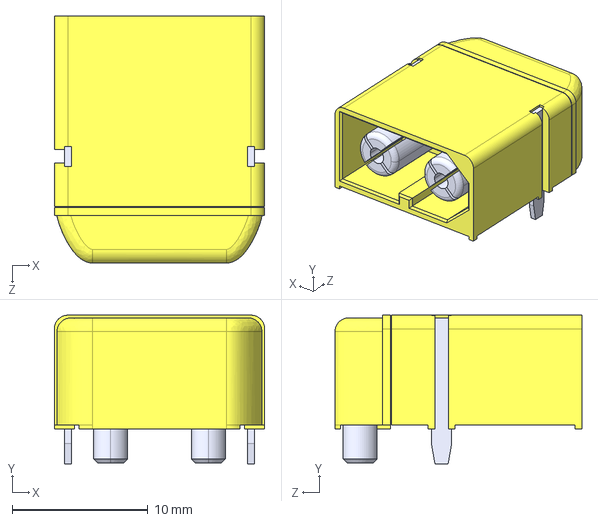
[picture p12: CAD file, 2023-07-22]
hw/dep/models/XT60PW-M.step
15.5 x 11.0 x 18.2 mm

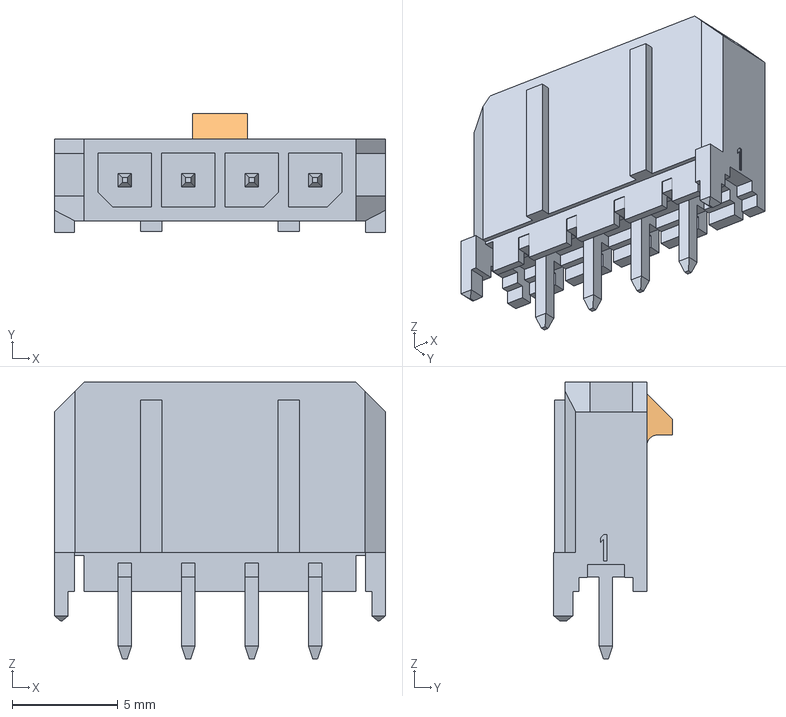
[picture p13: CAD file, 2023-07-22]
hw/models/molex_microfit_43650_0427.step
15.7 x 5.61 x 13.1 mm

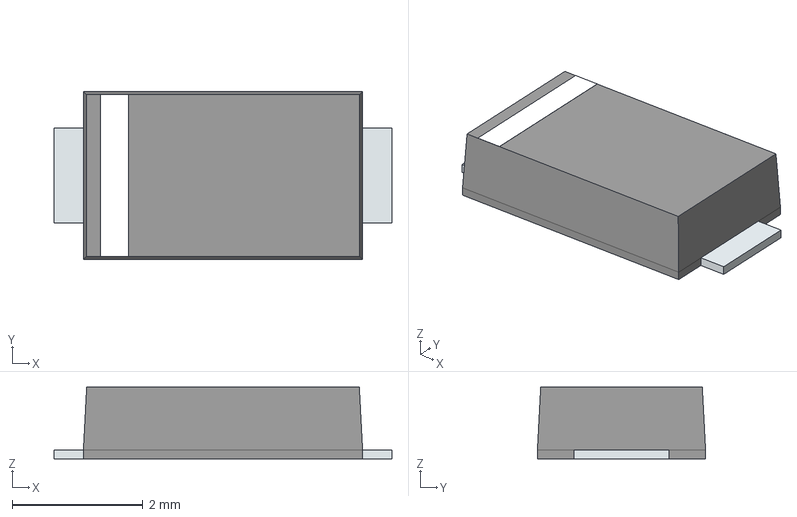
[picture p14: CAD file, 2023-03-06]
hw/dep/models/STPS1170AF.stp
5.17 x 2.58 x 1.10 mm
PinKIdent
PinK
PinA

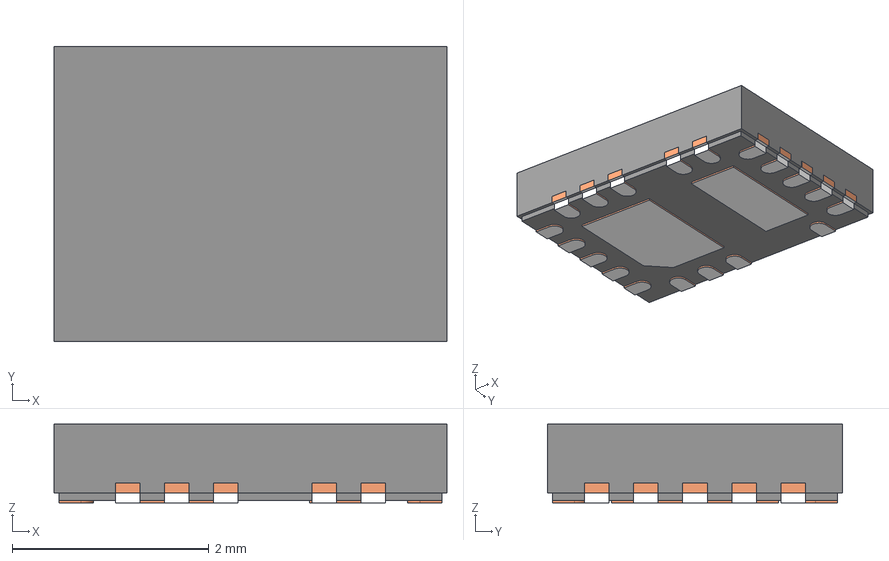
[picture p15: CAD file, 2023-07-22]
hw/models/ti_LMG1210RVRT.stp
4.00 x 3.00 x 0.8 mm
BODY-QFN_AF0
FRAME-RVR0019A_AF0
PIN1-ID

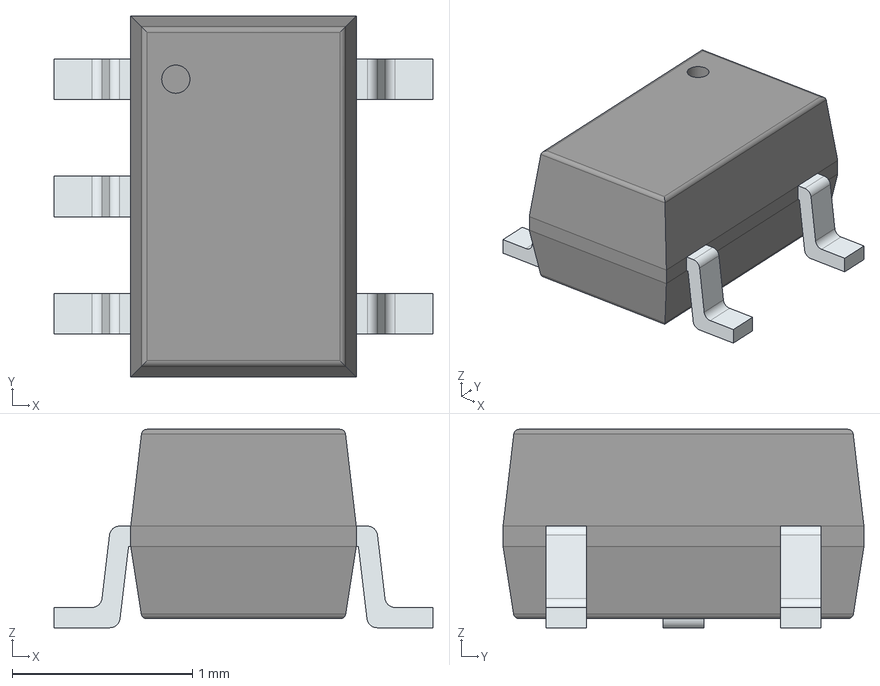
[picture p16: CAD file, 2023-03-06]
hw/dep/models/OPA990IDCKR.stp
2.10 x 2.00 x 1.10 mm
PinsArrayL
PinsArrayR

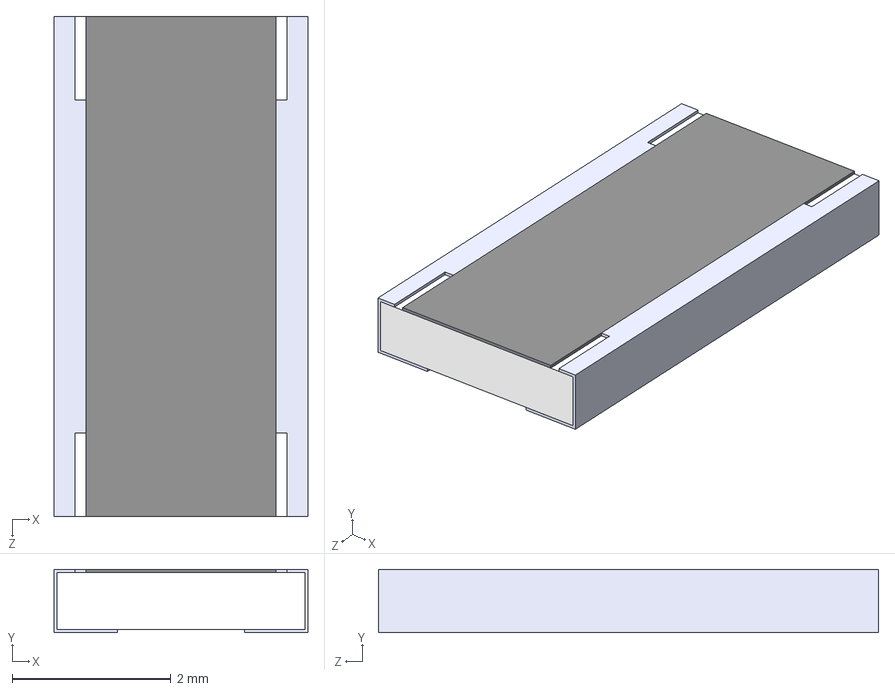
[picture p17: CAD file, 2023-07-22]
hw/models/vishay_THJP1225ABT1.STEP
3.20 x 0.8 x 6.30 mm

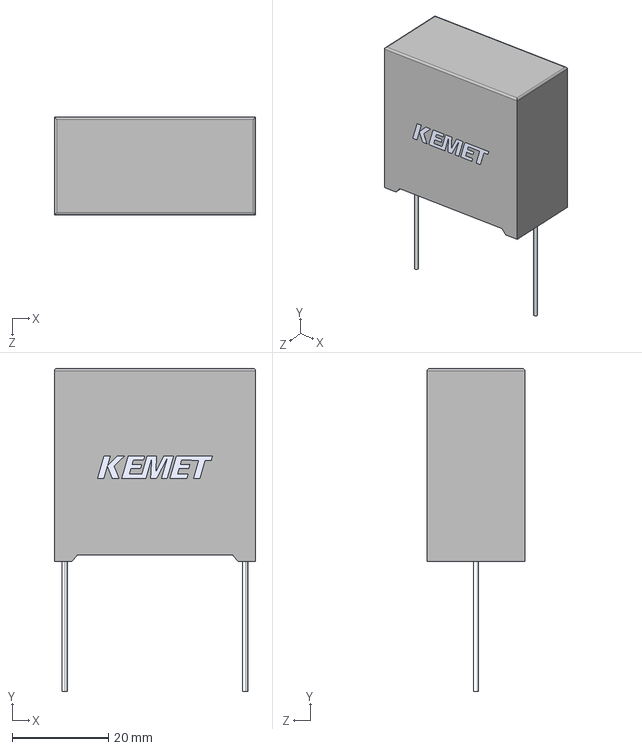
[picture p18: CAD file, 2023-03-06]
hw/dep/models/R75GW515050H0J.stp
41.8 x 67.1 x 20.3 mm

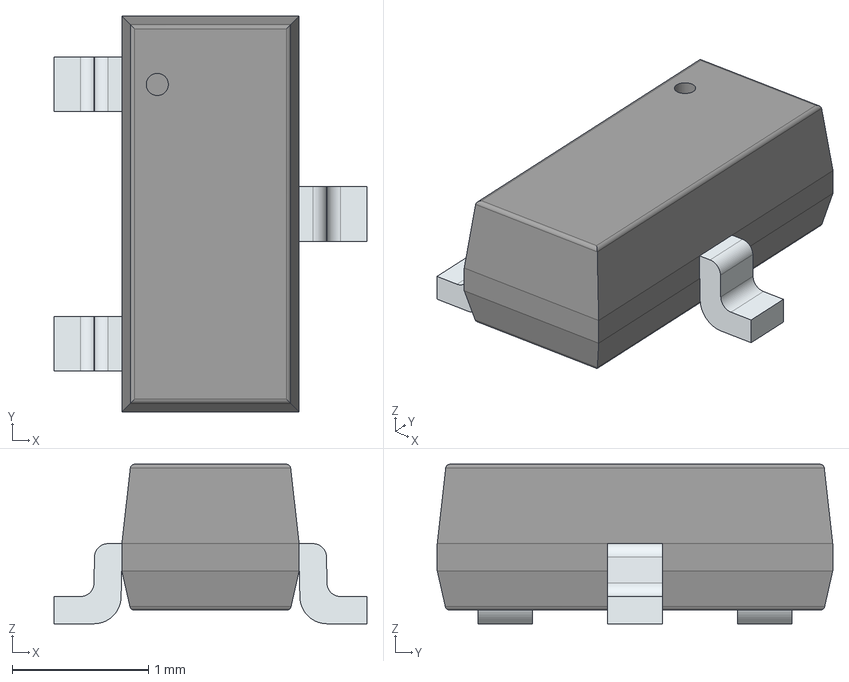
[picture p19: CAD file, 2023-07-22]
hw/models/bourns_CDSOT23_T24CAN.stp
2.29 x 2.90 x 1.17 mm
PinsArrayL
FilletPinR

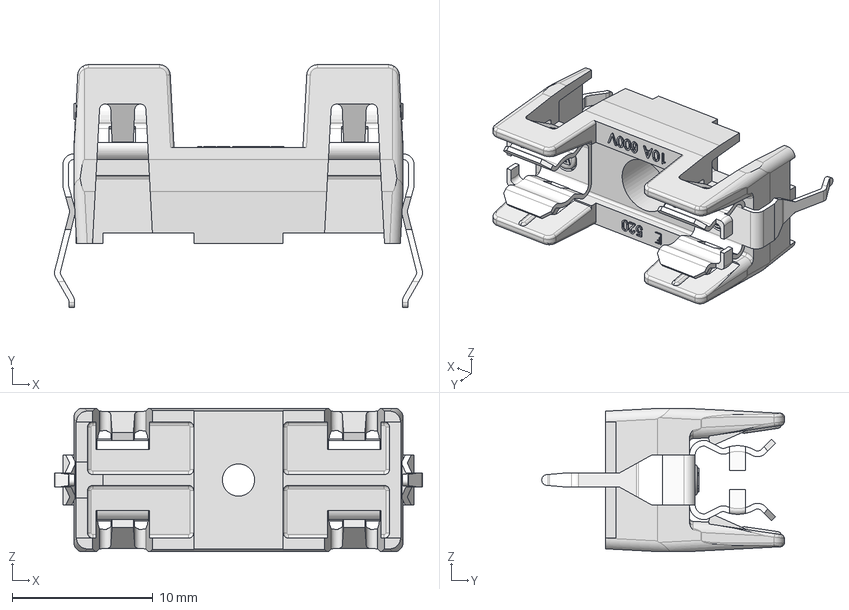
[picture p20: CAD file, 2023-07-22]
hw/models/littelfuse_05200101Z.stp
26.1 x 17.2 x 10.2 mm
111509_MIR

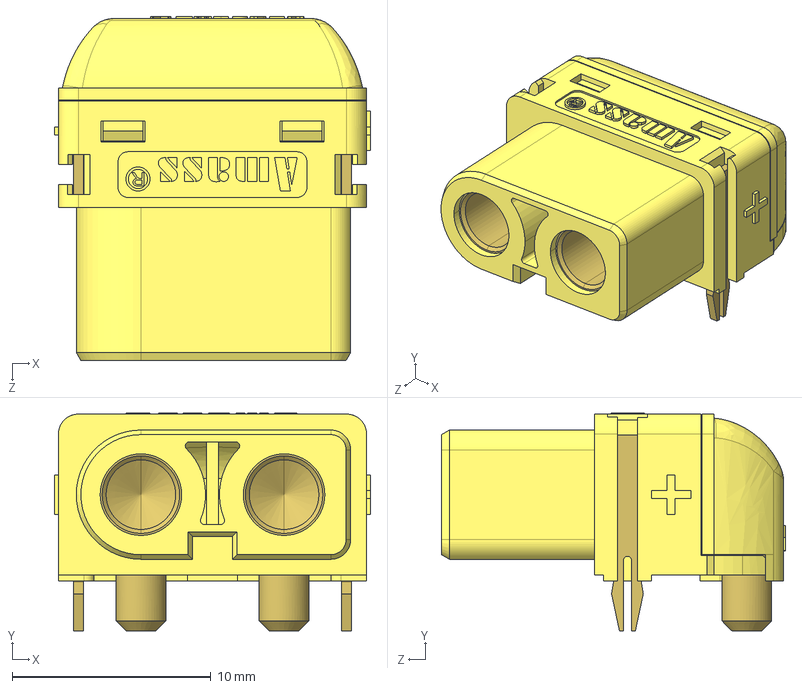
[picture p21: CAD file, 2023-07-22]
hw/models/amass_XT60PW_F.stp
15.9 x 11.0 x 17.3 mm

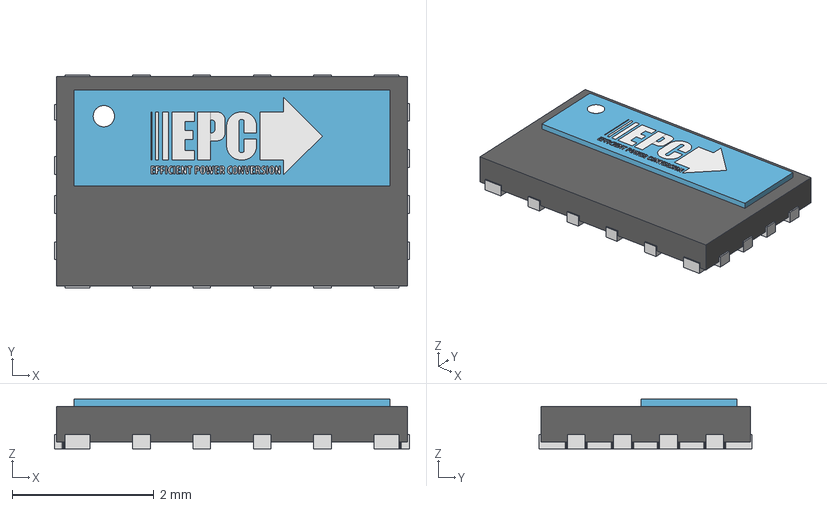
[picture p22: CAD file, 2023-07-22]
hw/models/epc_EPC2307.step
5.00 x 3.00 x 0.701 mm
3DEPClogo25mm
3DEPClogo25mm001
Extruded
Extruded001
Extruded002
Extruded003
Extruded007 x 4
Extruded008

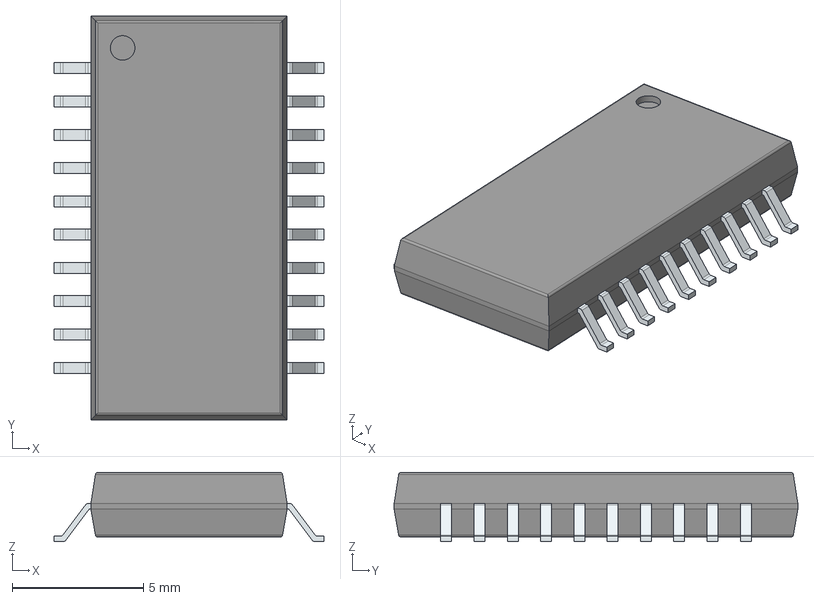
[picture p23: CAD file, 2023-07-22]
hw/models/analog_ADM3055EBRIZ.stp
10.3 x 15.4 x 2.64 mm
PinsArrayLR

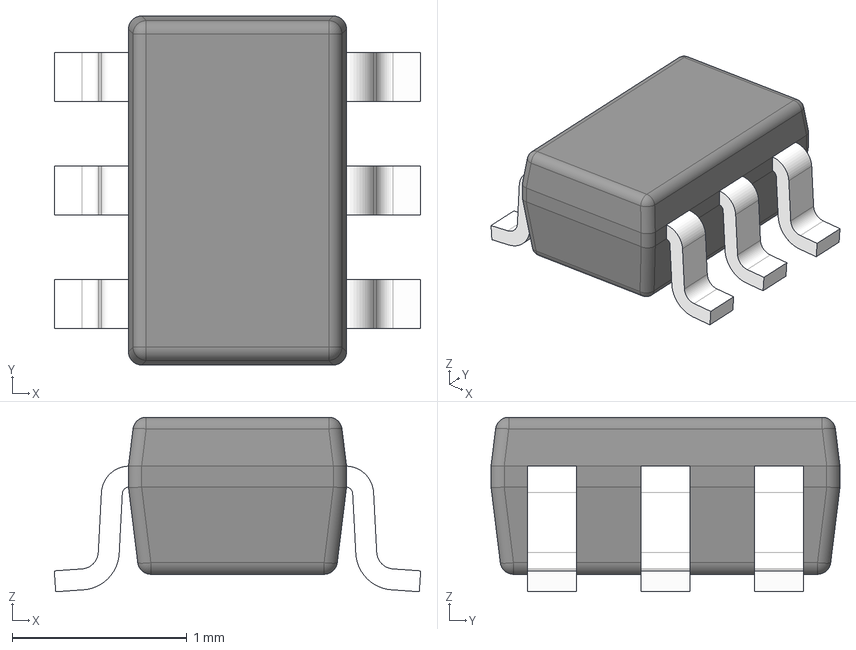
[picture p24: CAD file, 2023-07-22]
hw/models/ti_INA210CQDCKRQ1.stp
2.10 x 2.00 x 1.00 mm
BODY-SOT
LEAD-SOT x 6
PIN1-ID

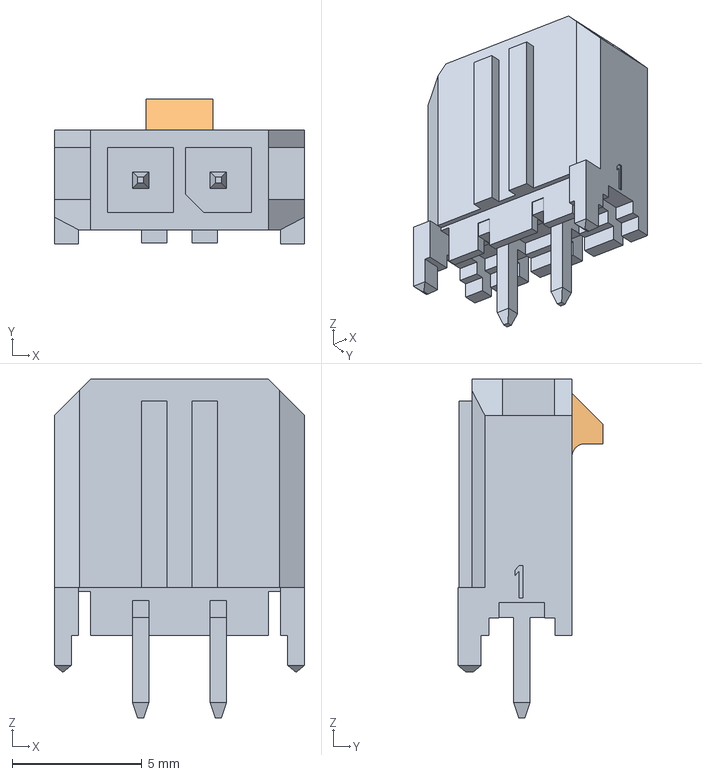
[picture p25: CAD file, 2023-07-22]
hw/models/molex_microfit_43650_0227.step
9.65 x 5.61 x 13.1 mm

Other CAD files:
hw/models/xkb_TS_1187A_B_A_B.step
hw/models/tdk_B65878E1012D001.stp
hw/dep/models/1935776.step
hw/dep/models/B32524R3156M000.stp
hw/dep/models/B65878E1012D001.stp

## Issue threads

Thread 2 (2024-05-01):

Propose v0.3.0 functional, safety, and performance requirements

dimembermatt, 2024-05-01:
From meeting notes:

# Safety
- temperature monitoring of high risk components
  - gate driver
  - FETs
  - inductor
- antisurge protection
  - resistor + high voltage  (max boost voltage * SF) diode path at switch node to handle voltage spike
     - yes it's a snubber circuit but no it's not supposed to be active during normal use
- extra hardware lockouts
- fan header support for additional active cooling (1W @ 12V) - M3 holes (default state on if unplugged)
- heat sink support for additional passive cooling
- potential new connector for ease of use and current capacity

# Functional
- swap down from Nucleo to chip (aim for 50% size reduction) (pull from existing team sch)
- USB C connector, DCDC regulator (isolated? or with reverse polarity protection)
- noniso CAN (pull from existing team sch)
- higher performance MCU -> aim for 200 MHZ
- dedicated ICs for current and voltage monitoring instead of the STM ADC
  - use I2C/SPI protocol
  - 12 bit
  - 100 kHz sampling rate
  - possibly autobuffer
- shrink pcb size

# Performance
- battery specs
  - 80V - 134V
  - use same model, assume 10A max input
- array specs
  - 0V - 80V VOC (25V - 70V, >100W)
  - 6.15A ISC
- 25% SF
- input inductor current ripple: N/A
- input capacitor voltage ripple: 1 V
- output capacitor voltage ripple: 1 V
- target efficiency: 99.5% at MPP

# Cost Estimate for 5 PCBS
- PCB
  - 4 Layer
  - 2oz copper
  - both sides assembly
  - ~200 - 250$
- Additional Components
  - 500$
- Labor
  - priceless (worthless)

150 USD per PCB

# Action Items
- 4/30: List of comprehensive tasks to be performed on optimization pipeline, simulation, sch/pcb, testing, etc (put on Github Project)
- 5/1: Preliminary schematic with BoM, begin initial review
- 5/4: Finalize schematic after full approval by (3) reviewers
- 5/4: Order initial test equipment
- 5/8: Preliminary layout, begin initial review
- 5/11: Finalize layout after full approval by (3) reviewers
- 5/12: Order pcbs and components
- 5/18: PCBs arrive, begin assembly
- 5/20: PCBs assembled, initial testing
- 5/30: Finish prelim testing, ship back to Austin

Closed 2024-05-01.

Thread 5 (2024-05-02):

Schematic: MCU template for STM32F446RETx

dimembermatt, 2024-05-02:
https://www.st.com/resource/en/datasheet/stm32f446re.pdf
https://www.st.com/resource/en/user_manual/dm00105823-stm32-nucleo-64-boards-mb1136-stmicroelectronics.pdf
https://www.st.com/resource/en/application_note/an1709-emc-design-guide-for-stm8-stm32-and-legacy-mcus-stmicroelectronics.pdf
https://www.st.com/resource/en/application_note/an4488-getting-started-with-stm32f4xxxx-mcu-hardware-development-stmicroelectronics.pdf

dimembermatt, 2024-05-03:
Update component blocks for the following peripherals:
- ADC
- SPI
- USB
- UART
- PWM
- CAN

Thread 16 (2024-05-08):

Define scope of SW optimization and simulation pipeline

dimembermatt, 2024-05-08:
What are the overarching goals and requirements for this project?

Given some **design specifications**, we want to
- find the optimal topology
  and components needed to build a converter that is:
  - maximally efficient
    - both broadly and
    - at maximum power transfer (the peak operating point)
  - maintains the desired safety factor
  - is within the specified input/output voltage/current ripple and
  - is effectively stable during open and closed loop operation
- visualize aspects of the optimal converter, including:
  - steady state operation, which involves input/output voltage
    mappings of:
    - duty cycle
    - current transfer
    - power transfer
    - losses across each component
    - temperature rise across each component
    - voltage and current ripple
    - efficiency
    - stability and time to settle within some statistical distribution
  - transient modeling of voltage and current nodes in response to some dynamic change.
- create a digital twin of a physical converter, that allows us to:
  - pair with different source/sink models
  - interface with higher level control models and
  - generate realistic dynamic simulations that can prove long duration
    efficiency and operation.

Based on the overarching goals, we have the following requirements:

- We shall be able to define requirements and operating
  specifications of the system, including:
  - the input and output model type and scope
  - the maximum acceptable input and output voltage and current
    ripple of the converter
  - the minimum acceptable stability of the converter
  - the minimum allowable safety factor of the converter
  - the maximum allowable cost and size budget of the converter

- We shall be able to provide a comprehensive and standardized set of components
  used in converter design, including the following:
  - FETs
  - schottky diodes
  - capacitors
  - inductors (cores + shape)

- We shall be able to select and design a converter from the
  following (but not exhaustive) list of topologies:
  - DC-DC converters
    - direct converter
      - asynchronous/synchronous buck/boost converter
      - four switch buck-boost converter
    - CCM and DCM operation
    - PFM operation
    - interleaved converters

Indirect DC-DC converters, DC-AC inverters, and AC-AC transformers are not
within the scope of this project.

- For each converter topology, we shall be able to identify a linear
  pathway for selecting components while minimizing the number of constraining
  variables.

- For each viable converter design (topology + components), we shall be able
  to generate estimated performance data in regards to the following attributes:
  - switching frequency
  - switch loss (switching versus conduction)
  - inductor loss (ripple versus conduction)
  - capacitor loss (ripple versus conduction)
  - switch temperature rise
  - inductor temperature rise
  - capacitor temperature rise
  - duty cycle
  - noise stability
  - component cost
  - component area

- For each viable converter design, we shall be able to assign a score or rank
  dependent on the estimated performance data, in particular:
  - total efficiency
  - total cost
  - total complexity (number of parts, distributors, etc)

- For each selected converter design, we shall be able to visualize its steady
  state and dynamic operation, including:
  - input/output maps of current, power transfer, efficiency, dead time, duty cycle
  - small signal stability analysis
  - large signal stability analysis
  - impulse response analysis

Sources:

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
- https://ocw.mit.edu/courses/6-334-power-electronics-spring-2007/888fe7fe65dbb6f11dc903f8caaa38f3_ch5.pdf
- https://www.eng.auburn.edu/~agrawvd/COURSE/READING/LOWP/Erikson_DC_2_DC.pdf
- https://www.e3s-conferences.org/articles/e3sconf/pdf/2017/04/e3sconf_espc2017_14010.pdf
- https://www.youtube.com/watch?v=1iq-YA2ivos

dimembermatt, 2024-05-08:
Breakdown of SW project

# Modularization of the pipeline

## specs package

Package specifying what our general design constraints
should look like.

- what is our expected input source model?
- what is our expected output sink model?
- what is our maximum allowable inp/out ripple?
- what is our minimum allowable safety factor?
- what is our target input/output ranges?
- (opt) what is our target power transfer?
- additional constraints
  - components that should not be used
  - maximum allowable cost
  - maximum number of parts distributors
  - etc

## source and sink package

Package specifying the types of sources and sinks that are
connected to the converter, and how they behave at various
operating regims.

## topology package

Package specifying the types of topologies that can be
implemented, as well as how to (1) linearly solve for a
solution and (2) relevant optimization parameters.

The topology package executes relevant component
subpackages and simulation subpackages.

List of converter topologies:

- async boost converter
- sync boost converter
- ...

## component package

Package specifying the various components that can be used
in the converters, and how to extract relevant parameters
from each of them.

- capacitors
- inductors
- FETs
- diodes

## simulation package

Package specifying the types of simulations that can and
should be performed for the topology, including:

- thermal simulation of components
- steady state efficiency
- small signal stability
- large signal stability
- etc

## graphics package

Package specifying the types of output graphics that can
and should be generated for the topology, including:

- input vs output maps
- etc

# Optimization of the pipeline

Using some combination of the following to improve
optimization and simulation time:
- numba
- cython
- multiprocess
- etc

# Expand component selection

Expand the existing CSVs to encompass required components.
Generate scraping scripts or automation scripts to extract
relevant properties.

If this requires narrowing manufacturers then so be it.

dimembermatt, 2024-05-26:
## specs package

Package specifying what our general design constraints
should look like.

- what is our expected input source model?
- what is our expected output sink model?
- what is our maximum allowable inp/out ripple?
- what is our minimum allowable safety factor?
- what is our target input/output ranges?
- (opt) what is our target power transfer?
- additional constraints
  - components that should not be used
  - maximum allowable cost
  - maximum number of parts distributors
  - etc

```json
{
    "NAME": "Broad range MPPT",
    "AUTHORS": ["Matthew Yu", "Jacob Pustilnik"],
    "DESCRIPTION": "MPPT Boost Converter v0.3.0",
    "DATE_DESIGNED": "05/23/24",
    "DESIGN": {
        "input_source": {
            "source_model_type": "solar_cell",
            "cell_type": "Maxeon Gen III Bin Le1",
            "num_cells": 111,
            "r_sh": 40,
            "r_s": 0.0035,
            "inp_ripple (V)": 1.0,
            "user_v_range": [20, 72]
        },
        "output_sink": {
            "sink_model_type": "battery",
            "battery_type": "INR21700-M50LT",
            "num_cells": 32,
            "out_ripple (V)": 1.0,
            "user_v_range": [80, 125]
        },
        "safety_factor": 1.2
    }
}

```

Closed 2024-05-26.

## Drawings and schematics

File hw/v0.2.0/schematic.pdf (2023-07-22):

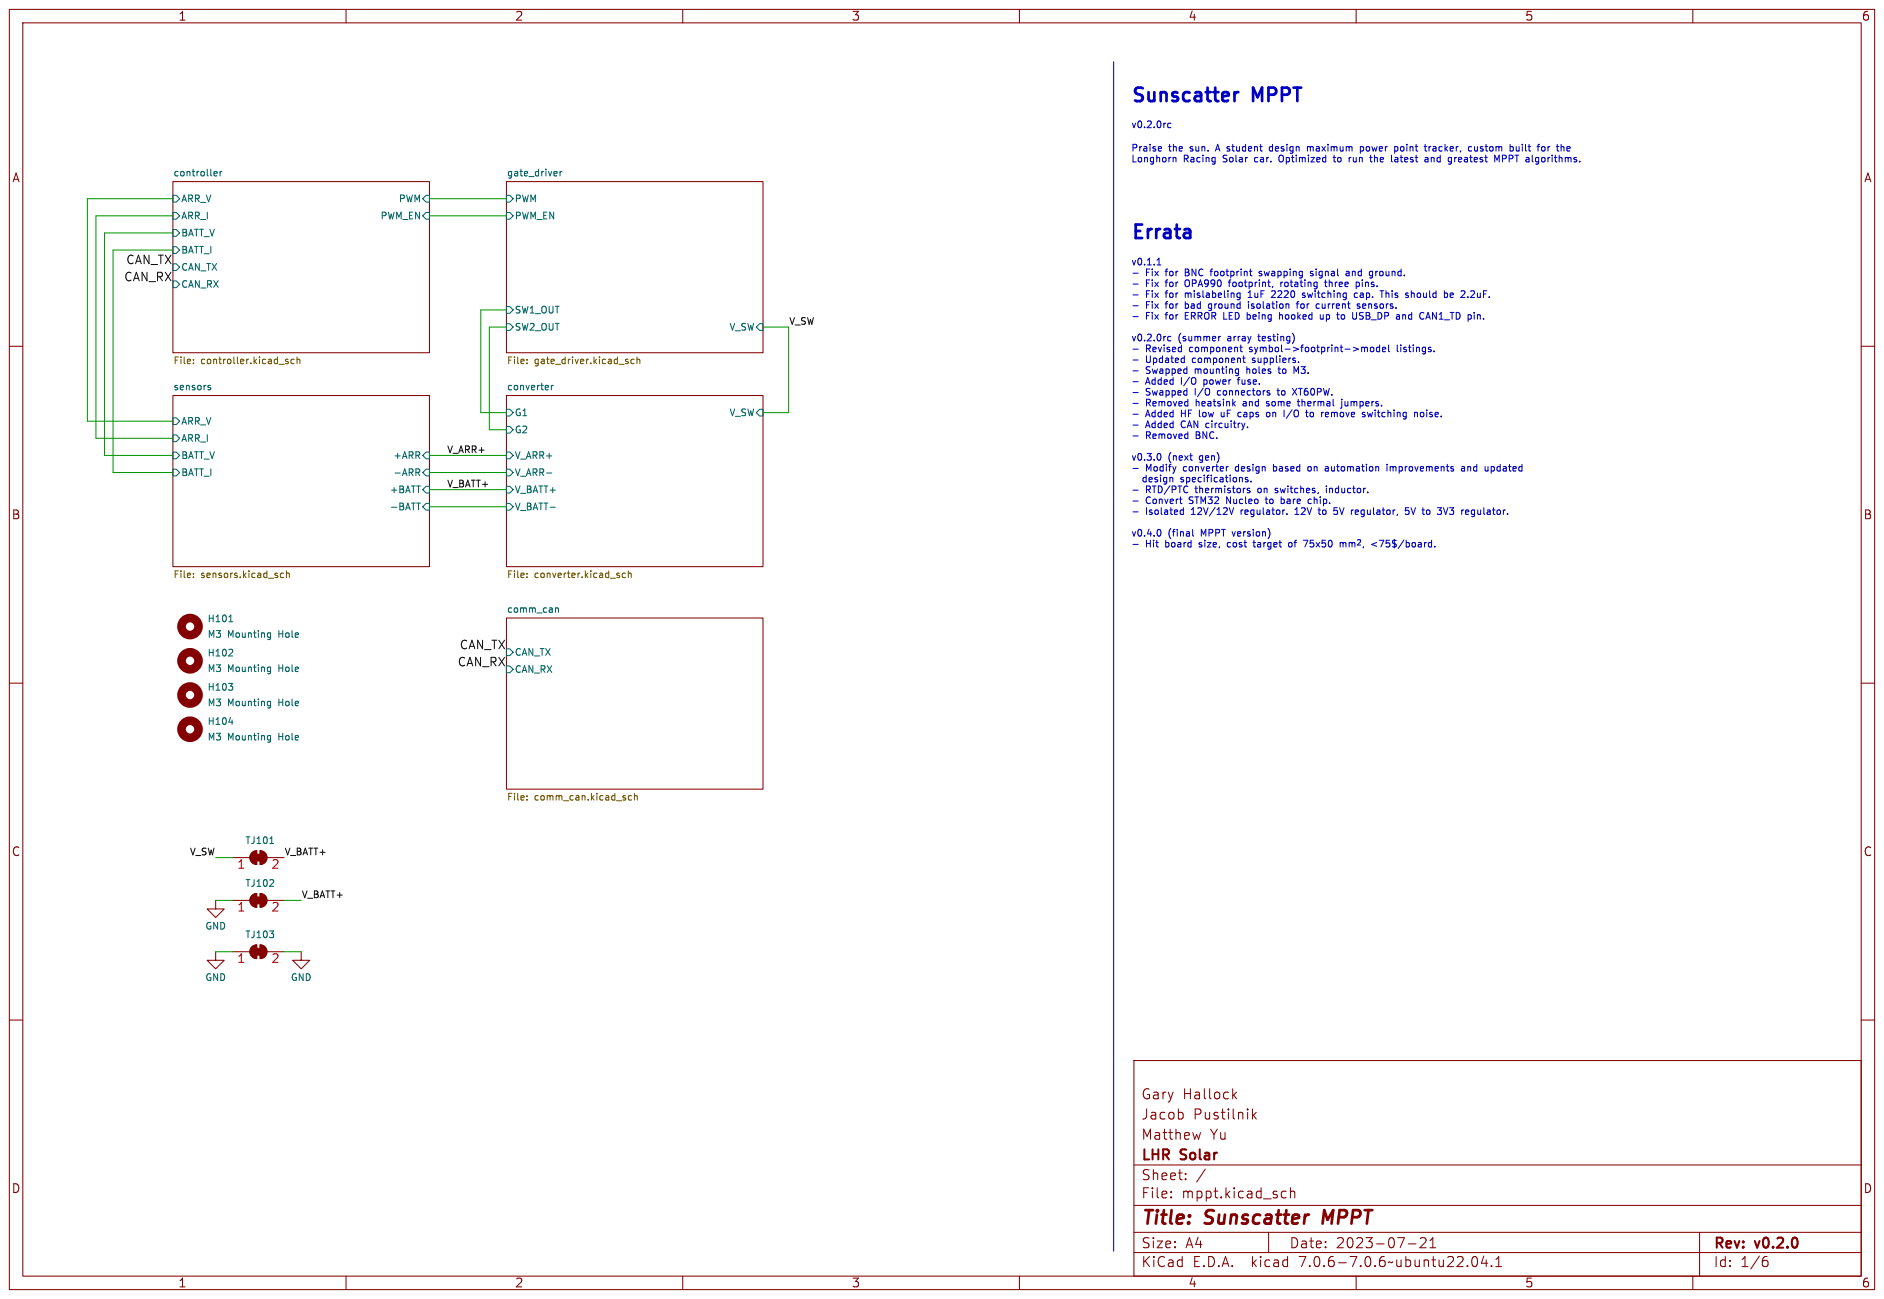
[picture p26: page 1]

- Hit board size, cost target of 75x50 mm^{2},<75$/board. Errata

File: mppt.kicad_sch Sheet: / LHR Solar Matthew Yu

Id: 1/6 Title: Sunscatter MPPT

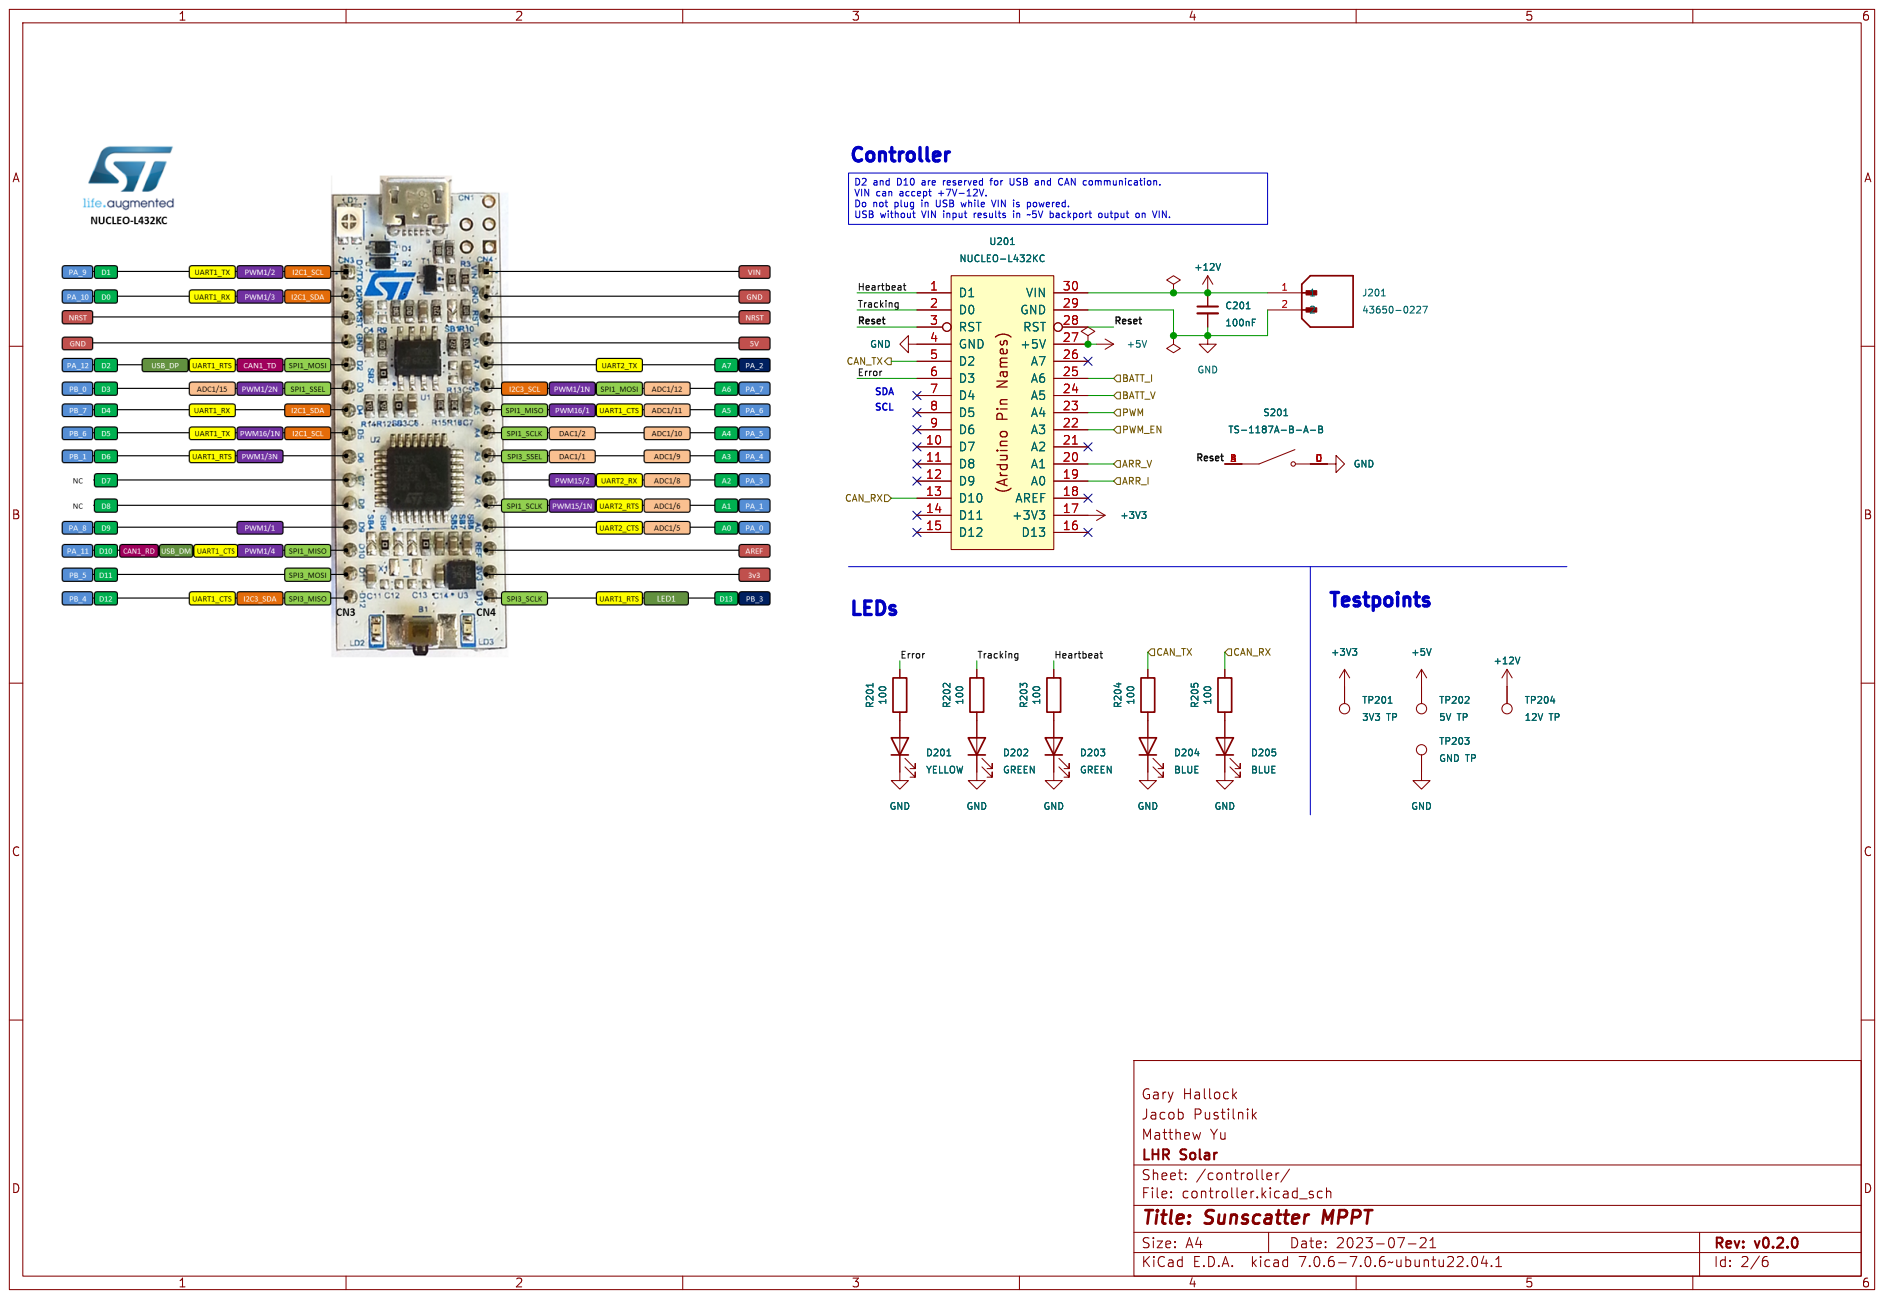
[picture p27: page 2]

File: controller.kicad_sch Sheet: /controller/ LHR Solar Matthew Yu

Id: 2/6 Title: Sunscatter MPPT

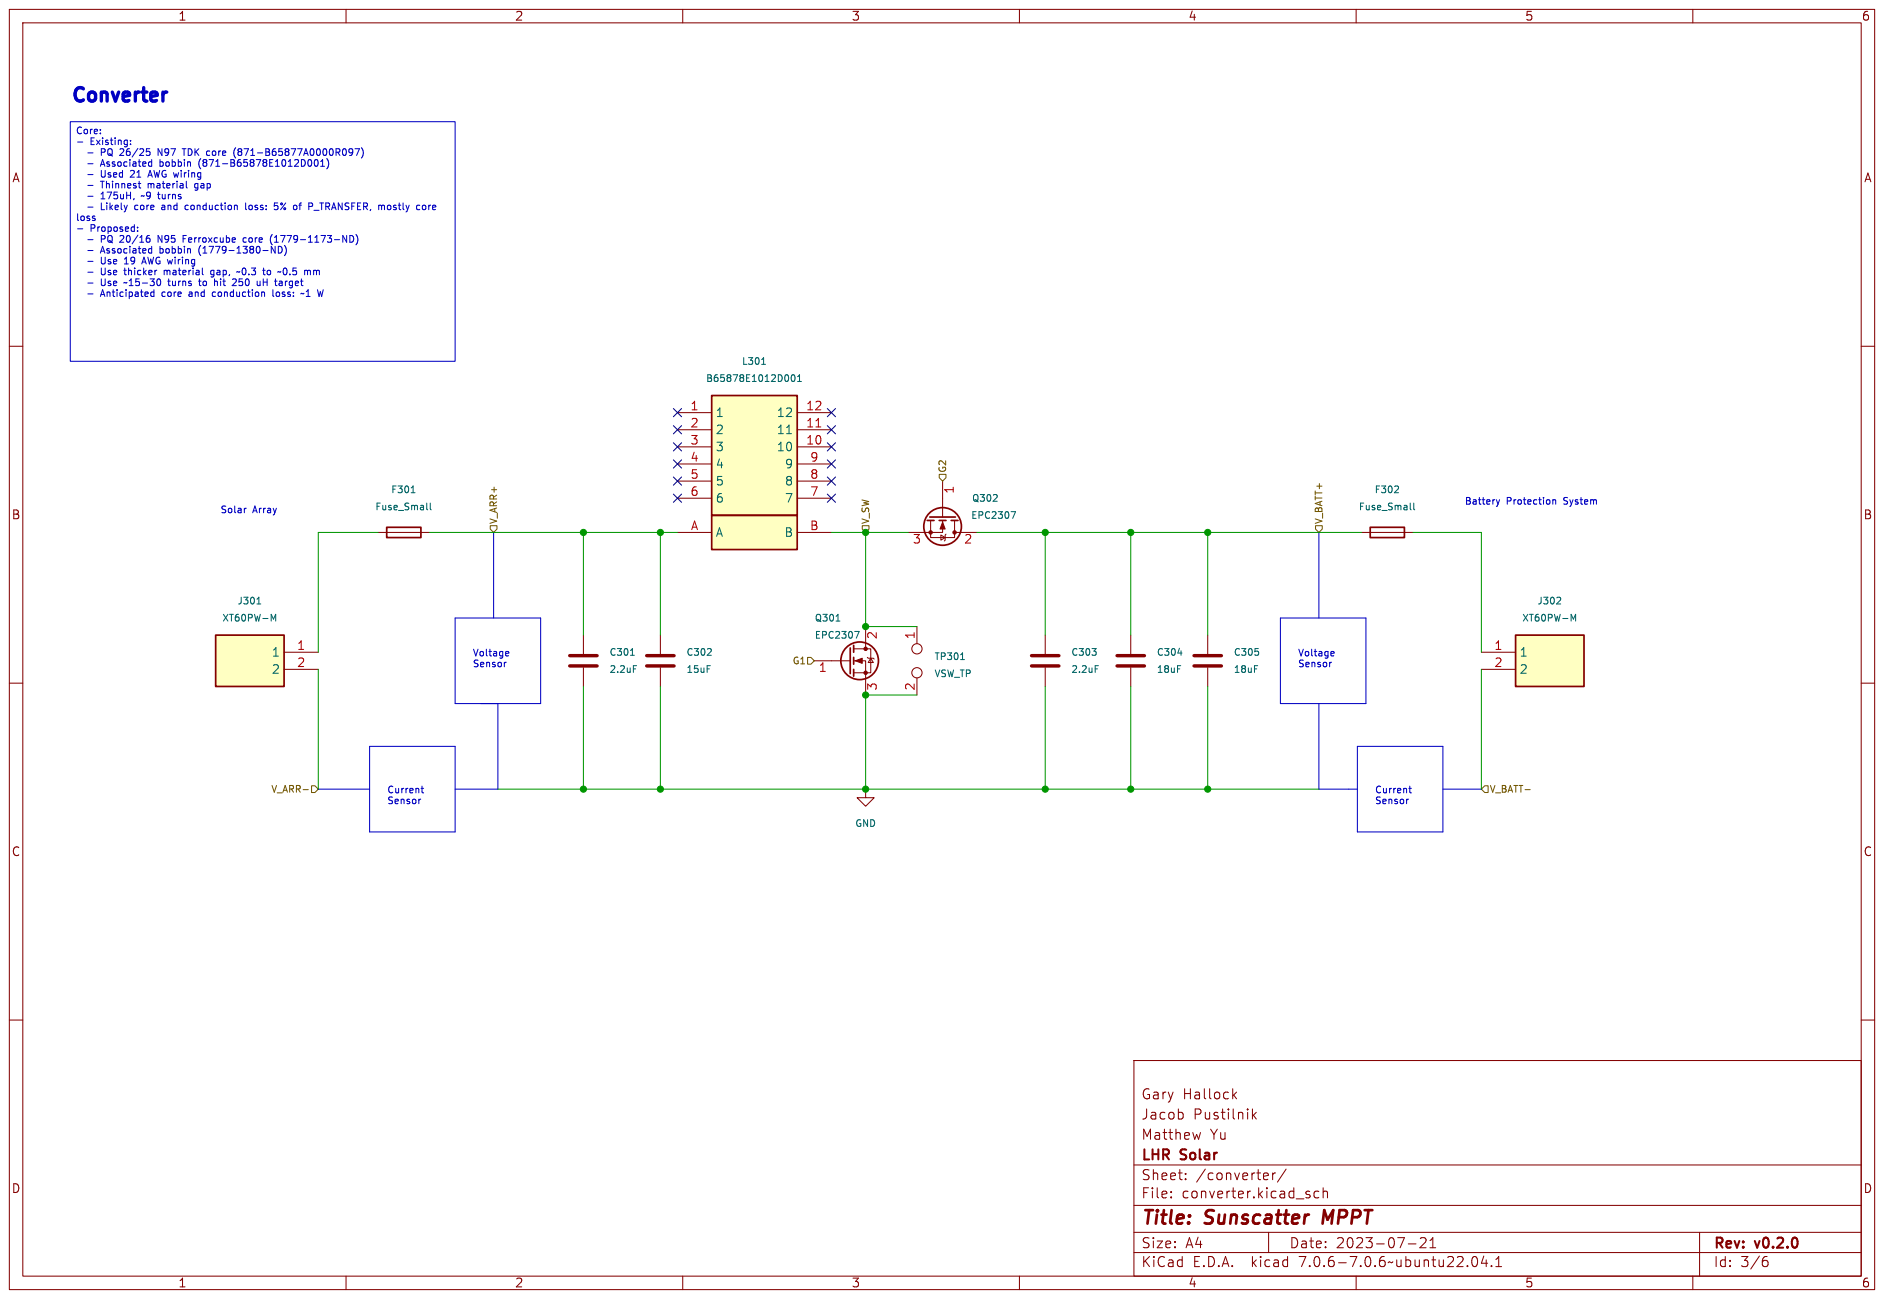
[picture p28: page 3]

Voltage Sensor

File: converter.kicad_sch Sheet: /converter/ LHR Solar Matthew Yu

Id: 3/6 Title: Sunscatter MPPT

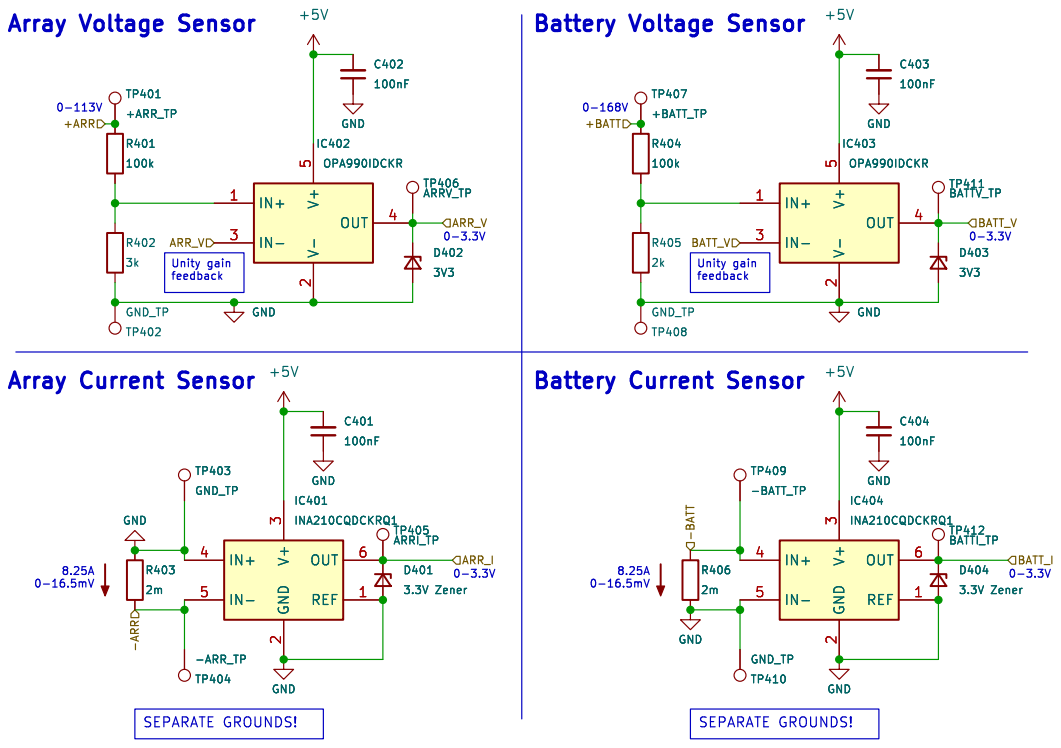
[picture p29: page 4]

File: sensors.kicad_sch Sheet: /sensors/ LHR Solar Matthew Yu

Id: 4/6 Title: Sunscatter MPPT

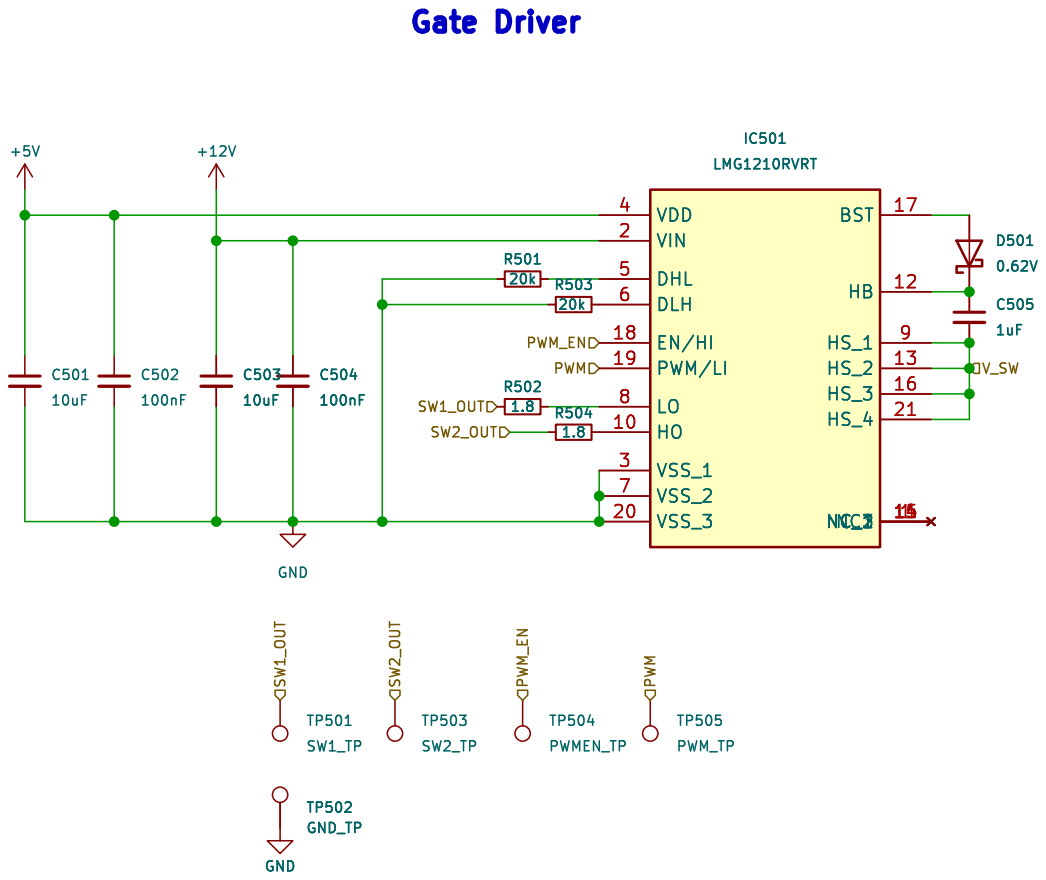
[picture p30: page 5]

File: gate_driver.kicad_sch Sheet: /gate_driver/ LHR Solar Matthew Yu

Id: 5/6 Title: Sunscatter MPPT

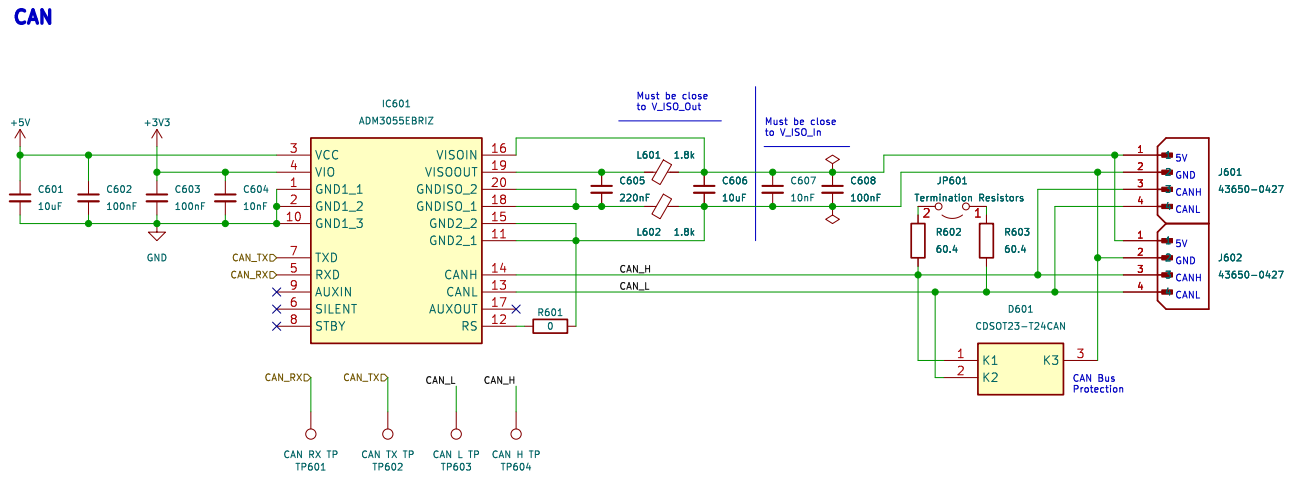
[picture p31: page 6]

File: comm_can.kicad_sch Sheet: /comm_can/ LHR Solar Matthew Yu

Id: 6/6 Title: Sunscatter MPPT

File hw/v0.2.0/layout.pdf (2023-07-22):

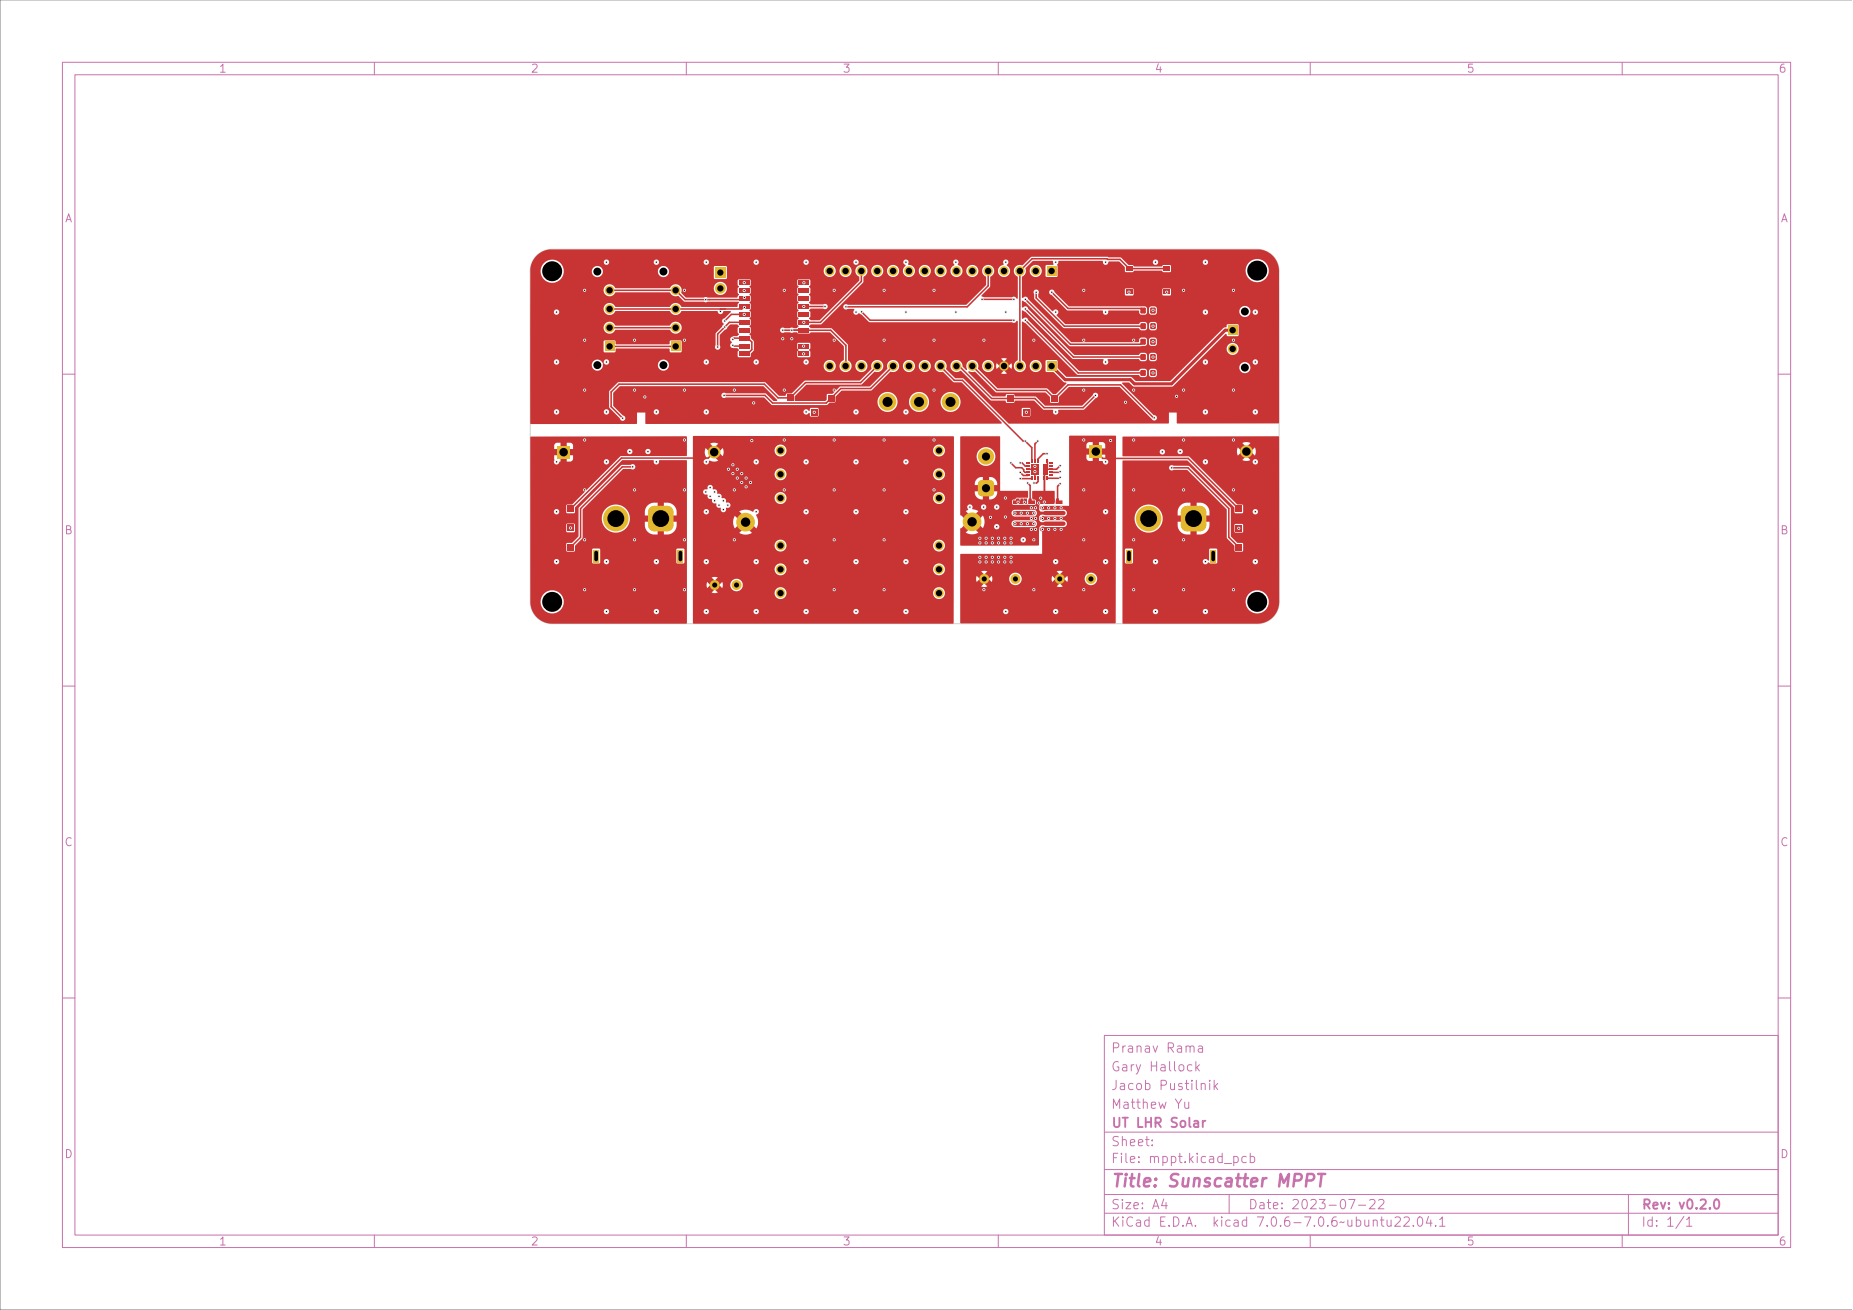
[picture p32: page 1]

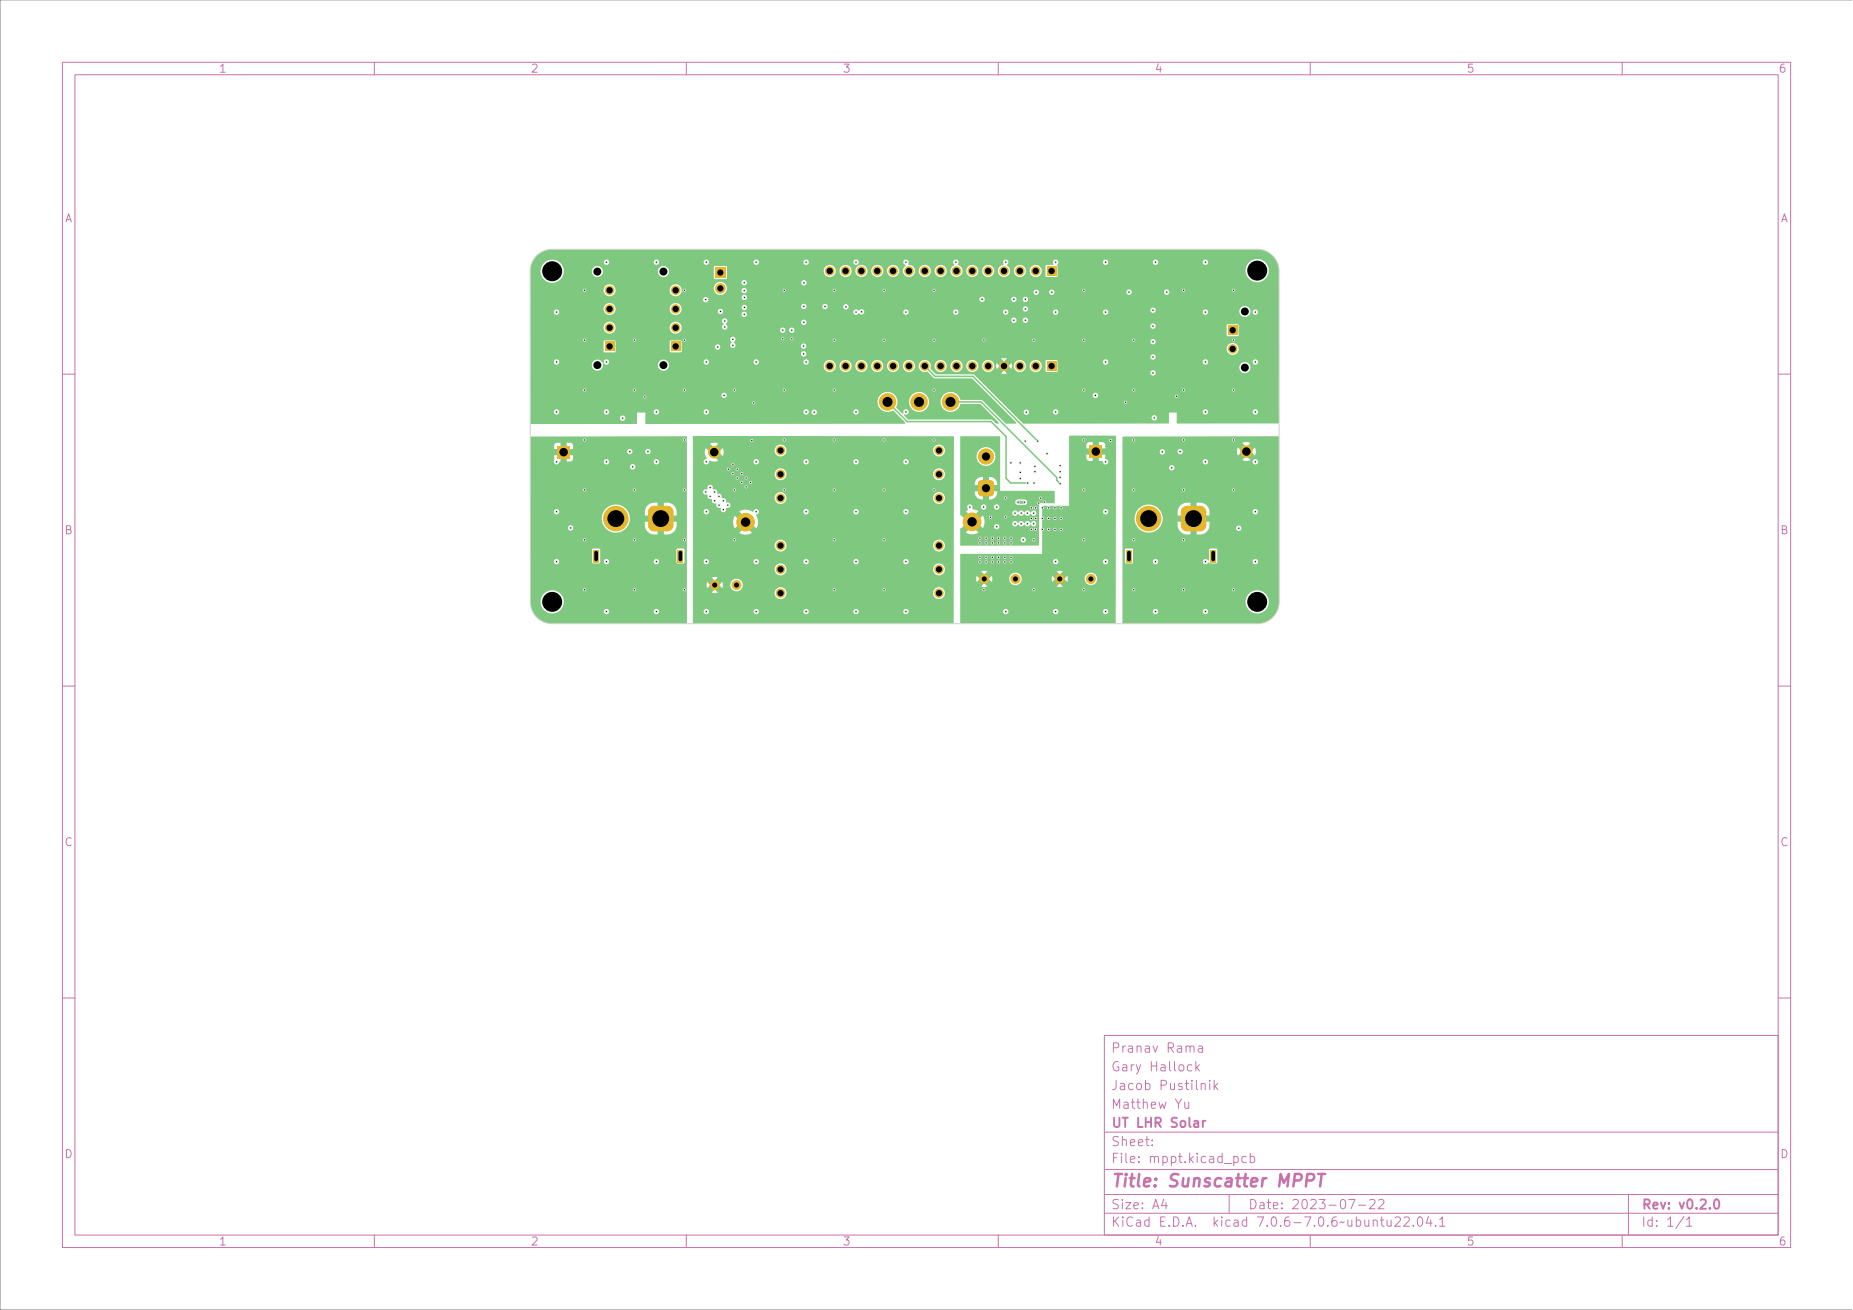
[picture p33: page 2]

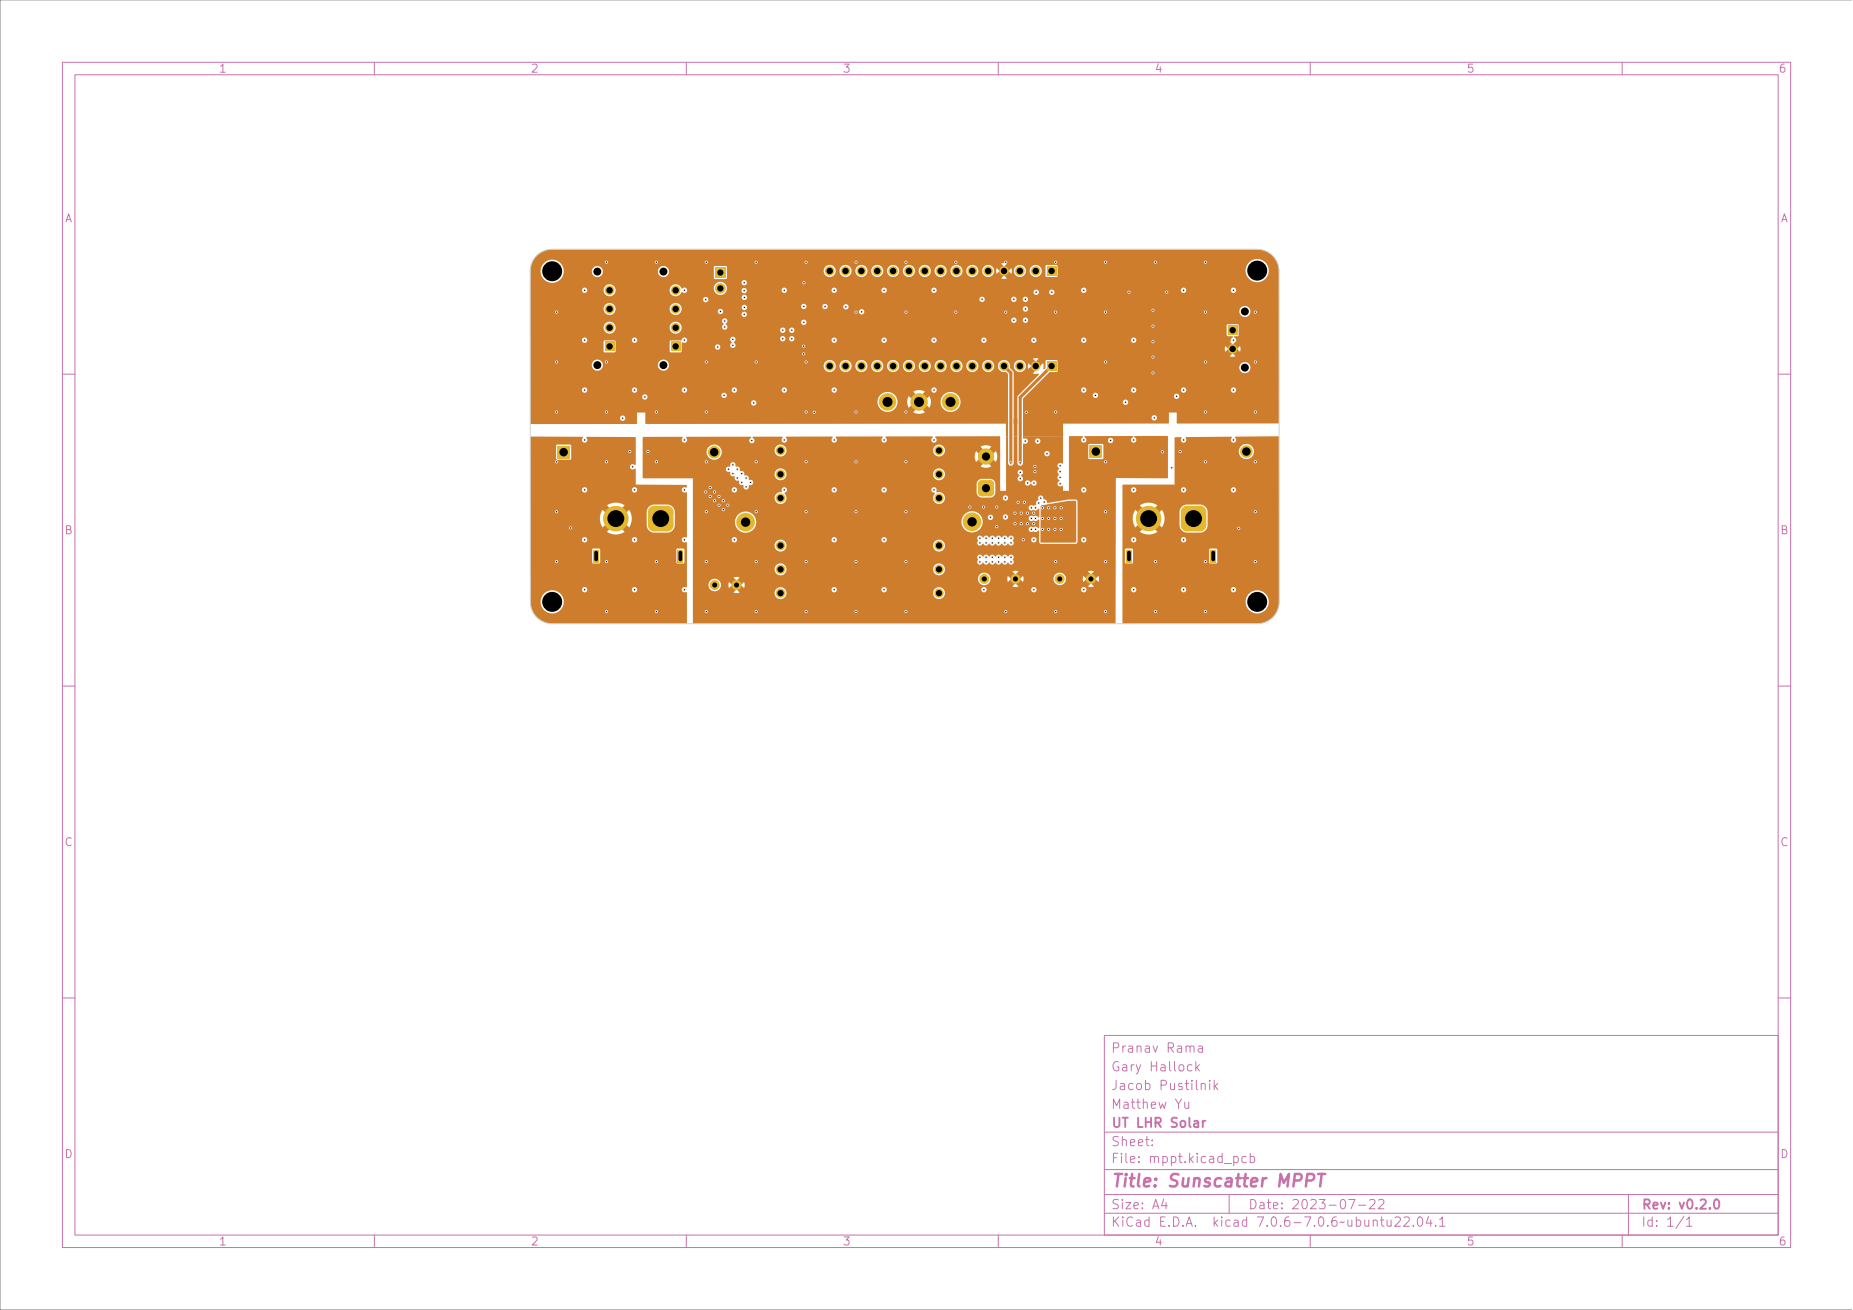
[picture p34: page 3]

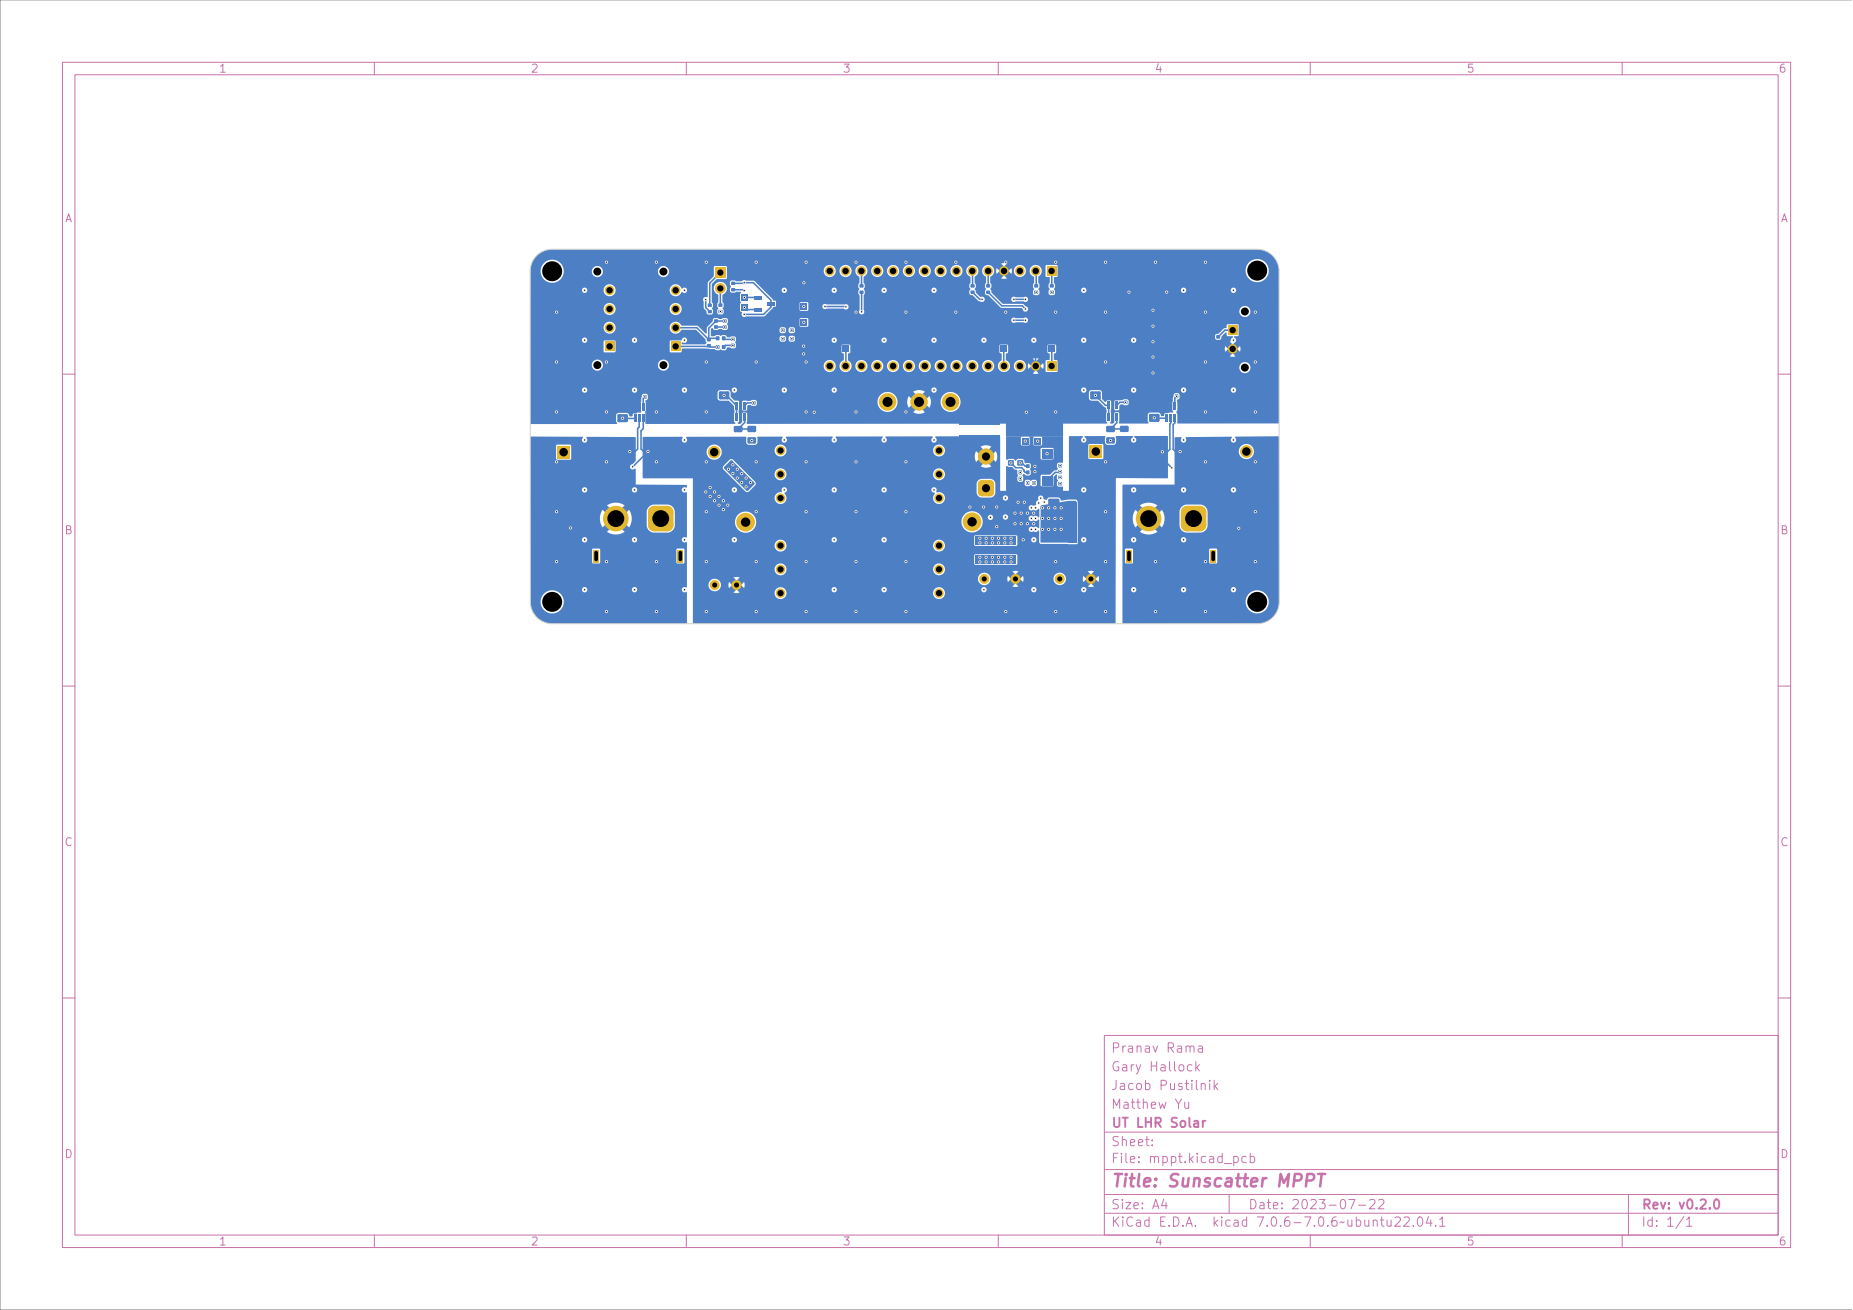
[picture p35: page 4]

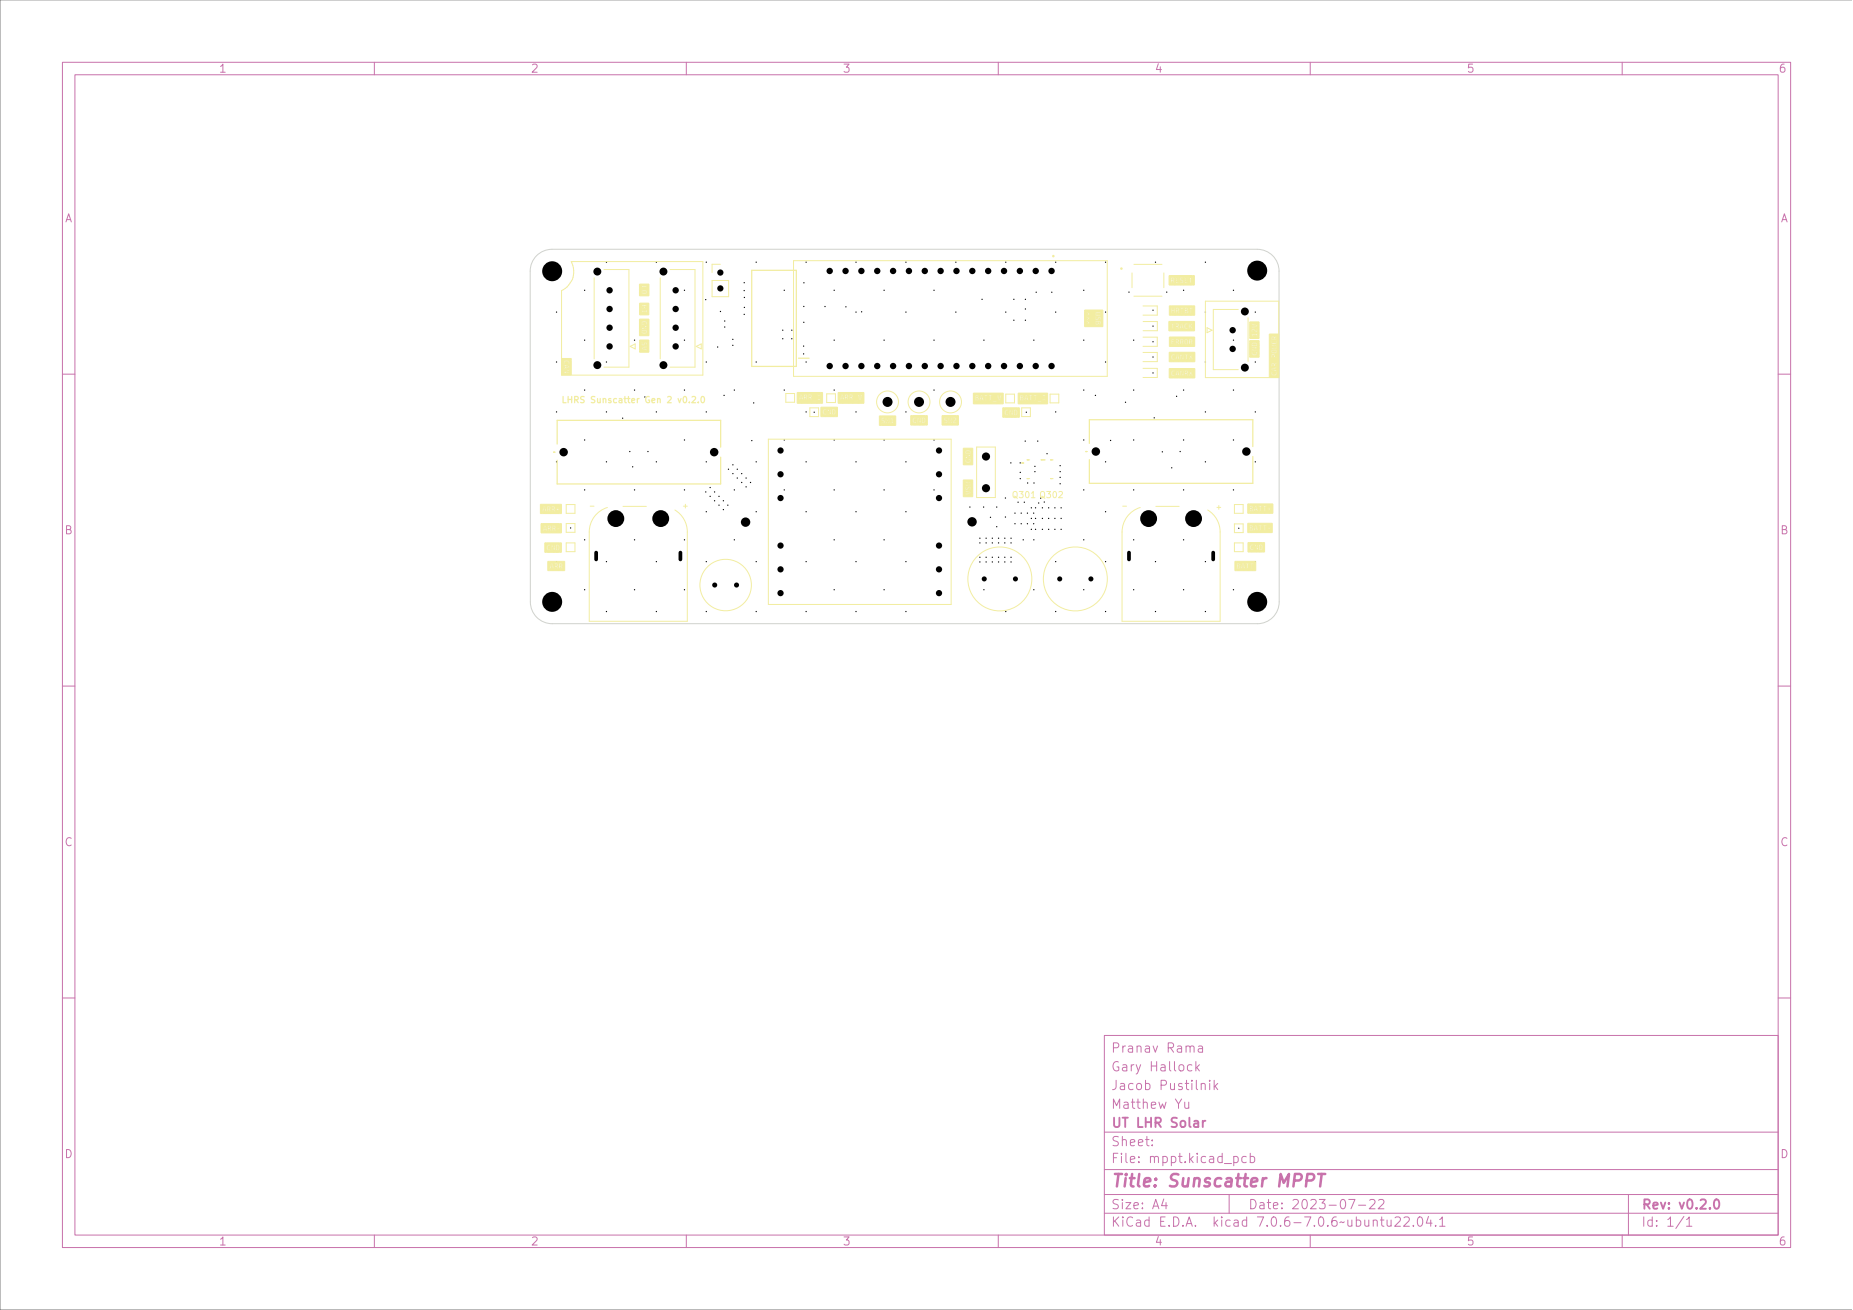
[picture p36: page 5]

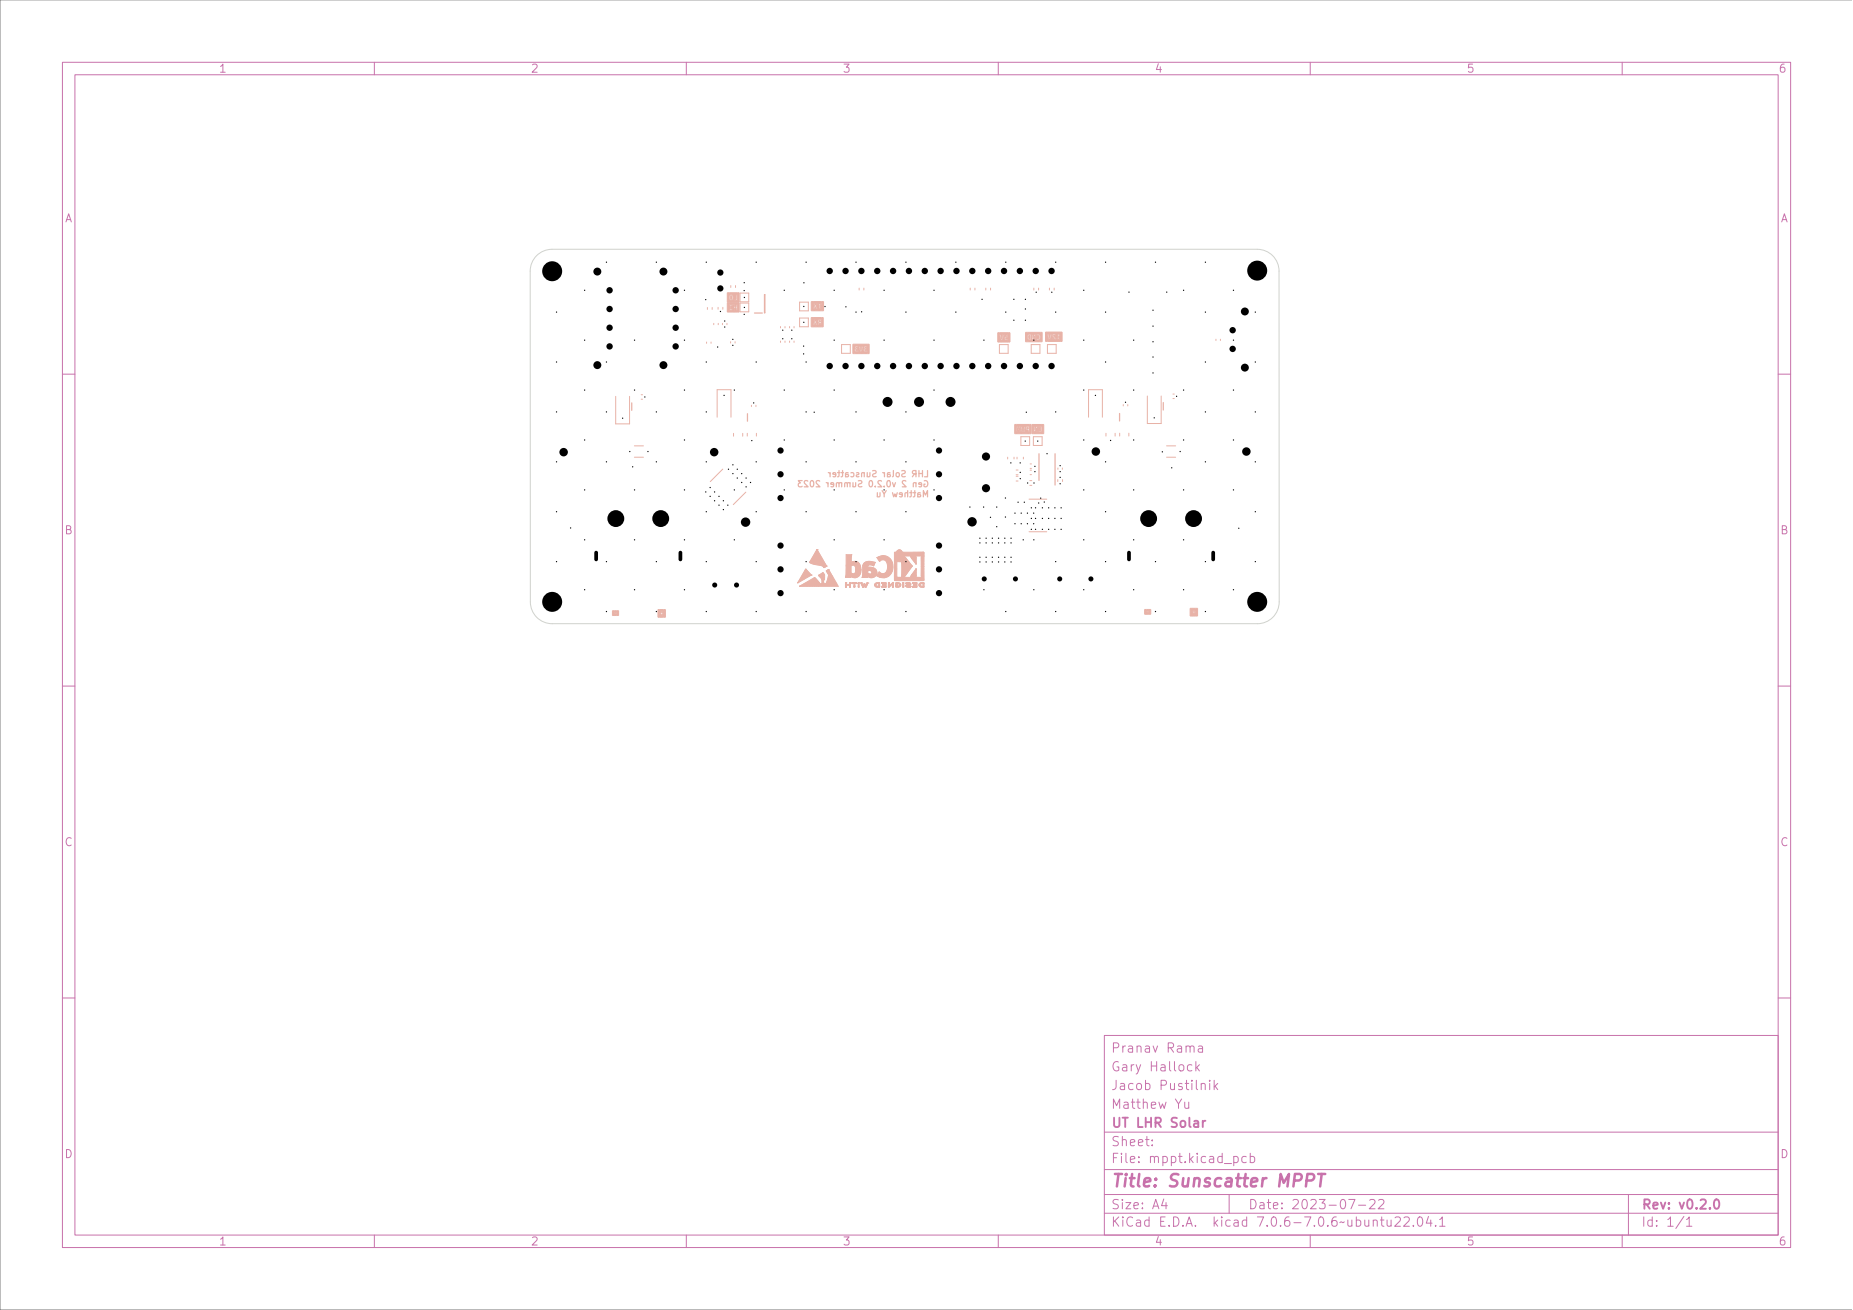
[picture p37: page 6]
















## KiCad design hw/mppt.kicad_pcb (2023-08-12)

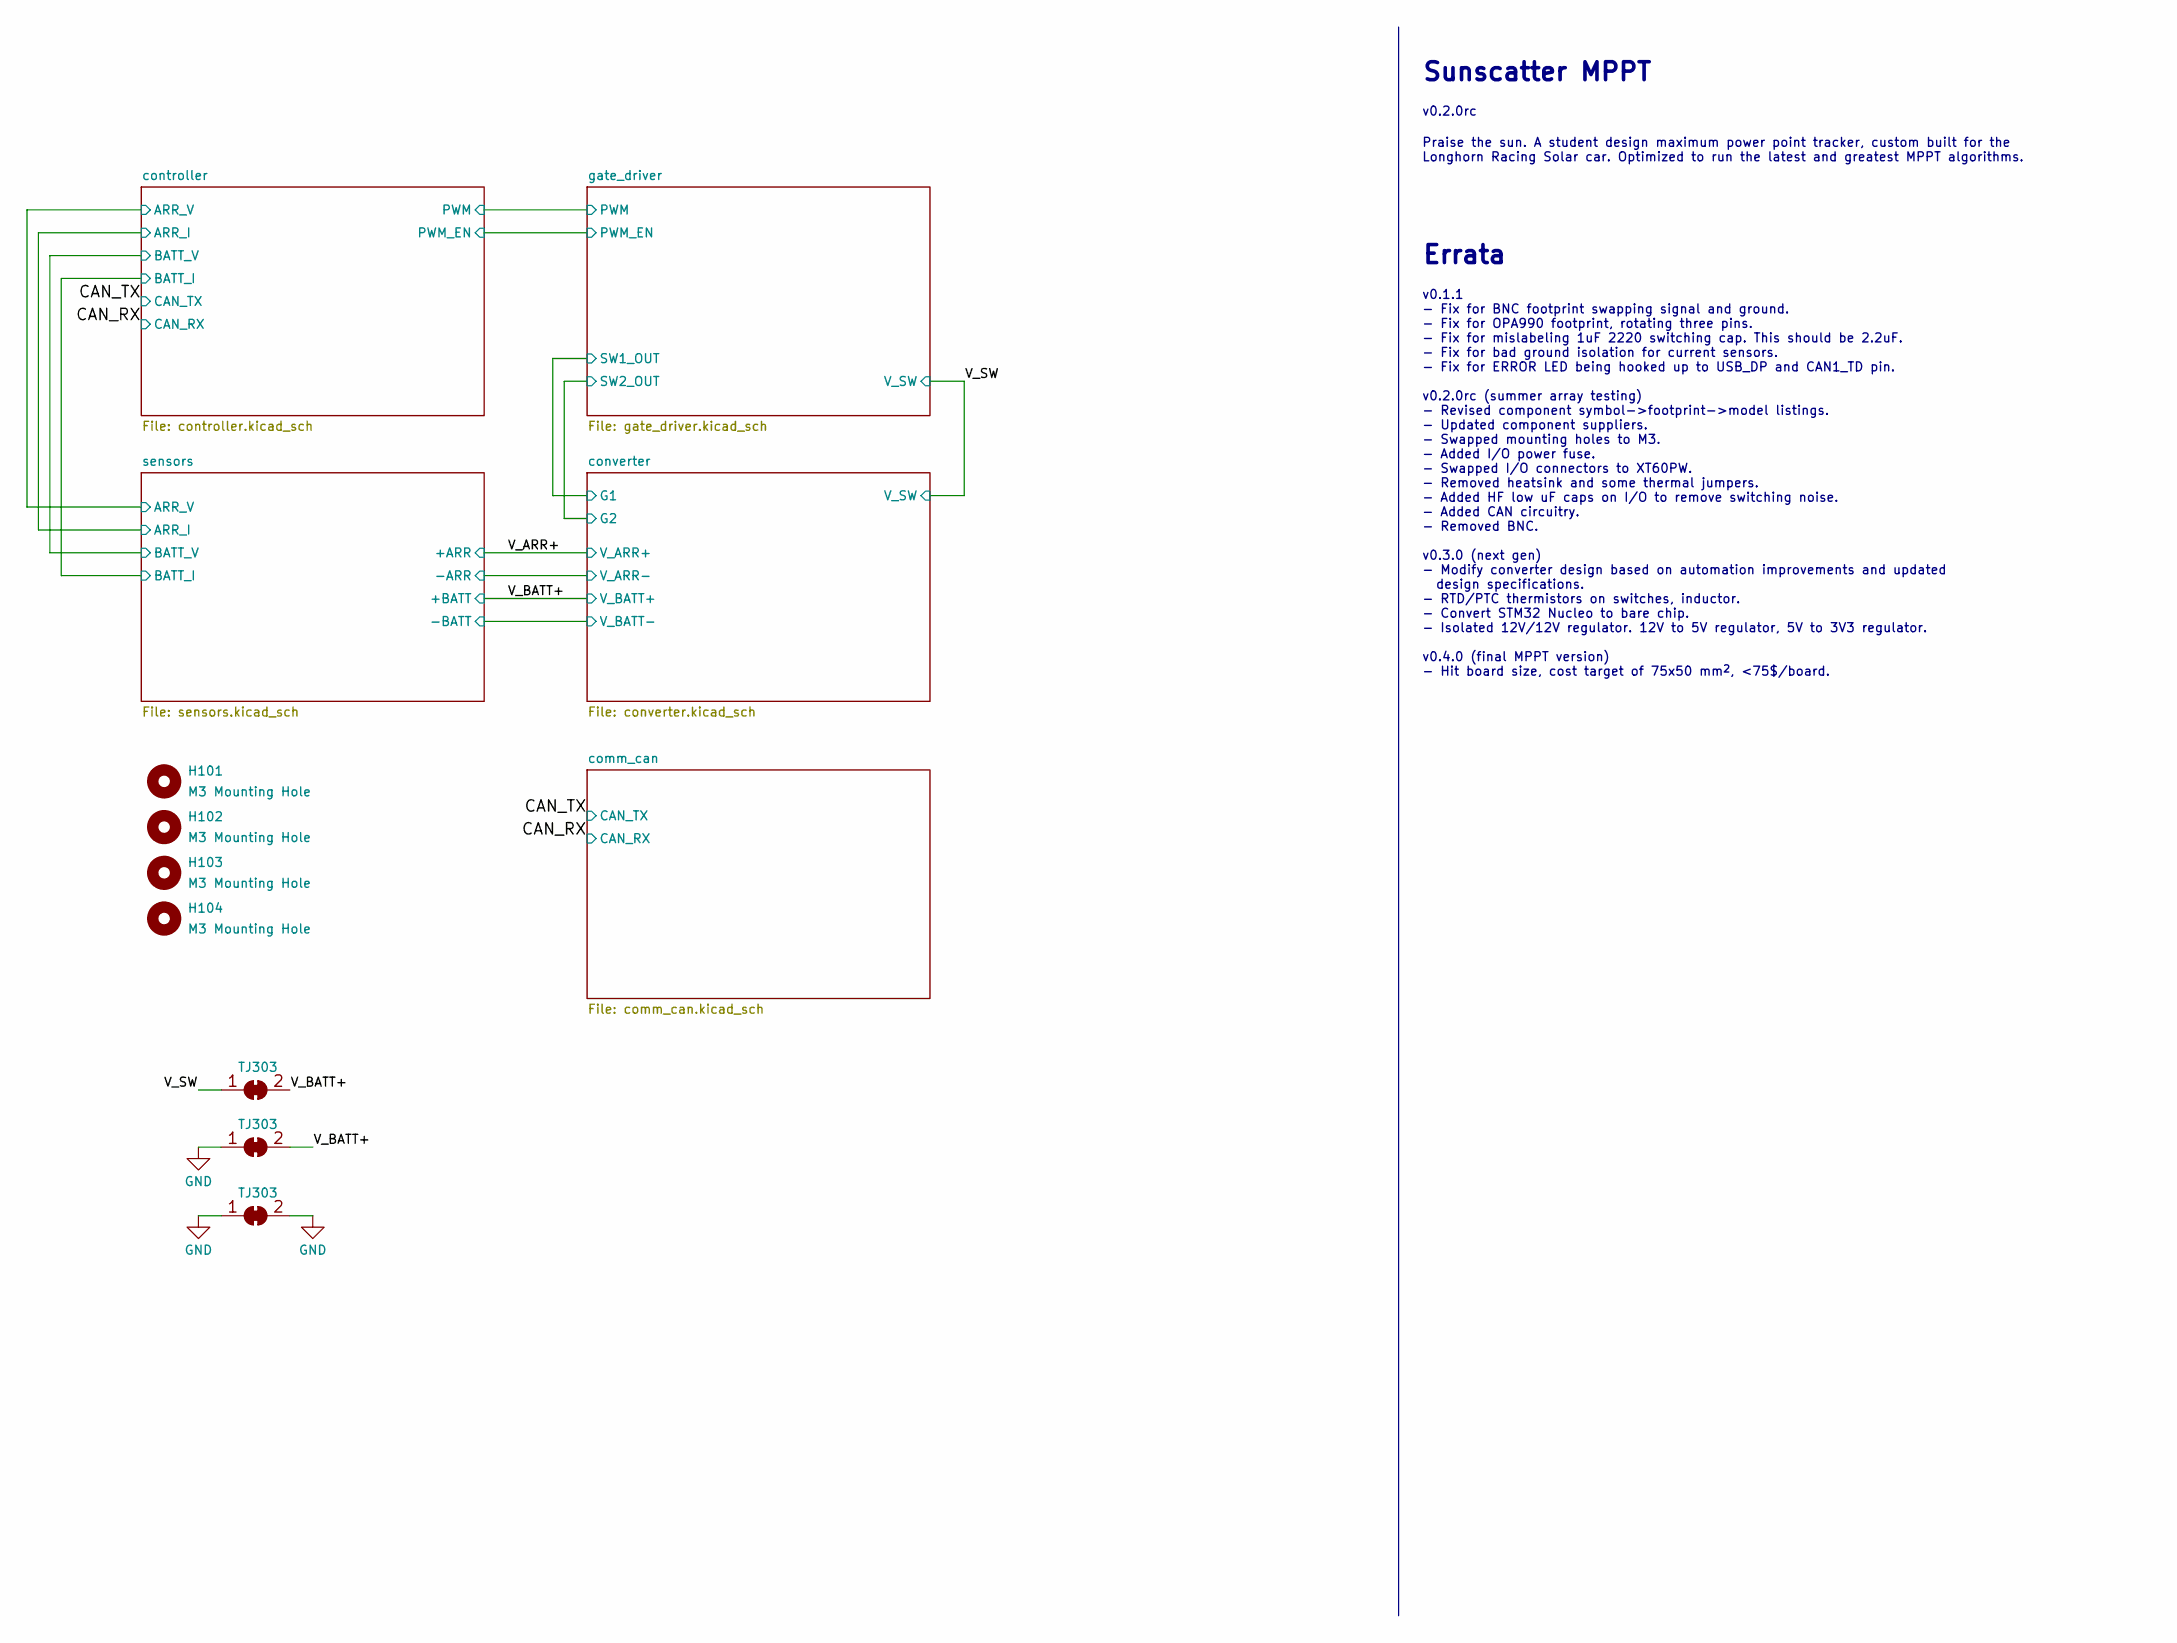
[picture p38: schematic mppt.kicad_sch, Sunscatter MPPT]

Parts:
H101, H102, H103, H104: M3 Mounting Hole; MountingHole_3.2mm_M3
TJ303: Thermal Jumper; vishay_THJP1225ABT1

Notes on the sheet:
Praise the sun. A student design maximum power point tracker, custom built for the Longhorn Racing Solar car. Optimized to run the latest and greatest MPPT algorithms.
Sunscatter MPPT
v0.2.0rc
Errata
v0.1.1 - Fix for BNC footprint swapping signal and ground. - Fix for OPA990 footprint, rotating three pins. - Fix for mislabeling 1uF 2220 switching cap. This should be 2.2uF. - Fix for bad ground isolation for current sensors. - Fix for ERROR LED being hooked up to USB_DP and CAN1_TD pin. v0.2.0rc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

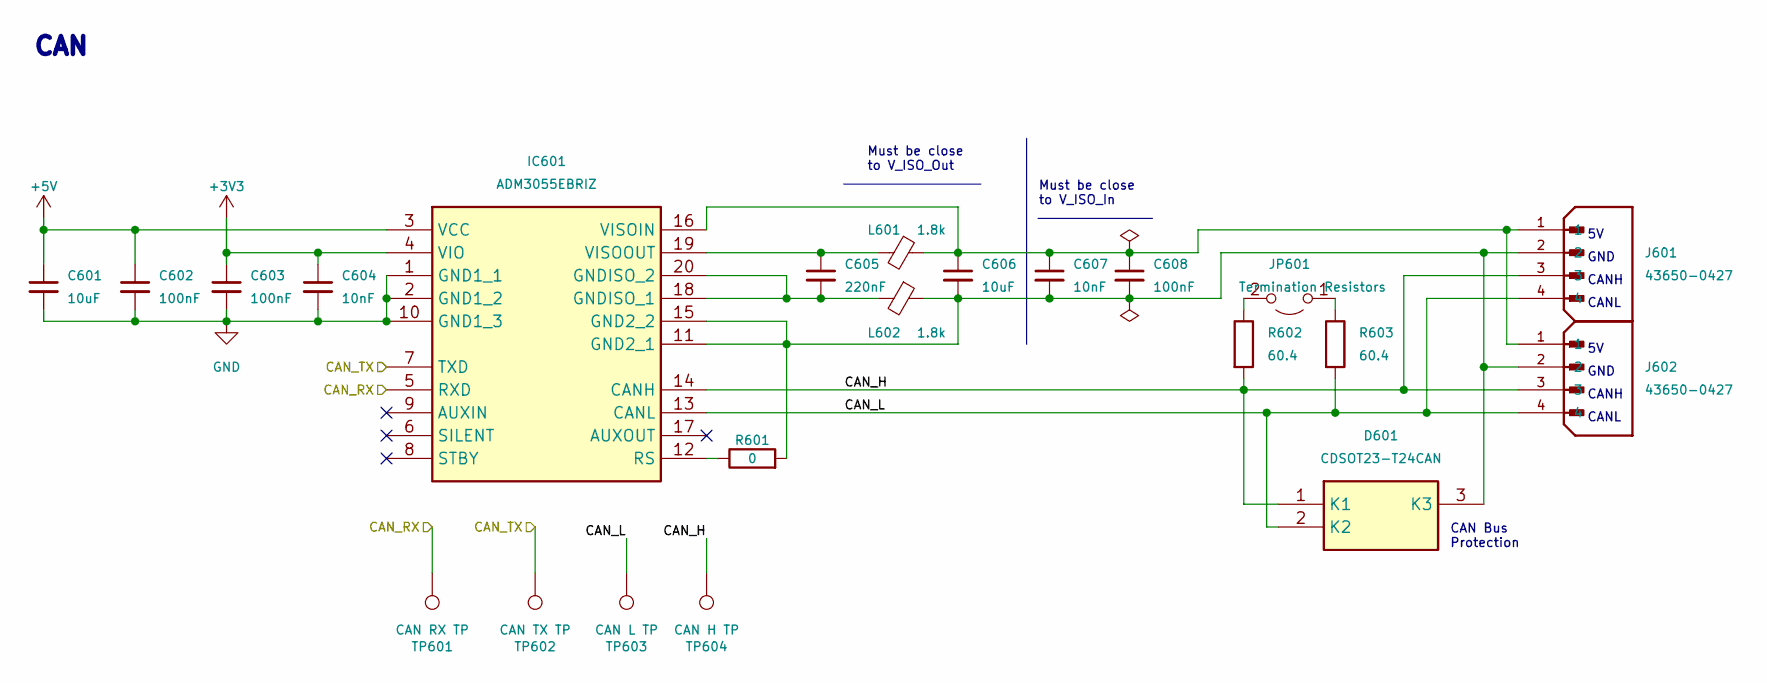
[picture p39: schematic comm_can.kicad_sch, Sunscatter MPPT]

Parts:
C601, C606: 10uF; C_0402_1005Metric; LCSC Part # C15525
C602, C603, C608: 100nF; C_0402_1005Metric; LCSC Part # CL05B104KB54PNC
C604, C607: 10nF; C_0402_1005Metric; LCSC Part # C15195
C605: 220nF; C_0402_1005Metric; LCSC Part # C16772
D601: CDSOT23-T24CAN; bourns_CDSOT23_T24CAN; LCSC Part # C350941
IC601: ADM3055EBRIZ; analog_ADM3055EBRIZ; LCSC Part # C658105
J601, J602: 43650-0427; molex_microfit_43650_0427
JP601: Termination Resistors; PinHeader_1x02_P2.54mm_Vertical
L601, L602: 1.8k; L_0402_1005Metric; LCSC Part # C2683172
R601: 0; R_0402_1005Metric; LCSC Part # C17168
R602, R603: 60.4; R_0402_1005Metric; LCSC Part # C60310
TP601: CAN RX TP; TestPoint_Pad_1.0x1.0mm
TP602: CAN TX TP; TestPoint_Pad_1.0x1.0mm
TP603: CAN L TP; TestPoint_Pad_1.0x1.0mm
TP604: CAN H TP; TestPoint_Pad_1.0x1.0mm

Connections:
+3V3: C603.1, C604.1, IC601.4 (VIO); also elsewhere on the board
/CAN_RX: IC601.5 (RXD), TP601.1; also elsewhere on the board
/CAN_TX: IC601.7 (TXD), TP602.1; also elsewhere on the board
/comm_can/CAN_H: D601.1 (K1), IC601.14 (CANH), J601.3, J602.3, R602.2, TP604.1
/comm_can/CAN_L: D601.2 (K2), IC601.13 (CANL), J601.4, J602.4, R603.2, TP603.1
GND: C601.2, C602.2, C603.2, C604.2, IC601.1 (GND1_1), IC601.2 (GND1_2), IC601.10 (GND1_3); also elsewhere on the board
unnamed: C606.2, C607.2, C608.2, D601.3 (K3), IC601.11 (GND2_1), IC601.15 (GND2_2), J601.2, J602.2, L602.1, R601.2
unnamed: C605.2, IC601.18 (GNDISO_1), IC601.20 (GNDISO_2), L602.2
unnamed: IC601.12 (RS), R601.1
unnamed: C606.1, C607.1, C608.1, IC601.16 (VISOIN), J601.1, J602.1, L601.1
unnamed: C605.1, IC601.19 (VISOOUT), L601.2
unnamed: JP601.1 (A), R603.1
unnamed: JP601.2 (B), R602.1

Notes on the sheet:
CANL
CANH
GND
CAN Bus Protection
CAN
Must be close to V_ISO_In
Must be close to V_ISO_Out

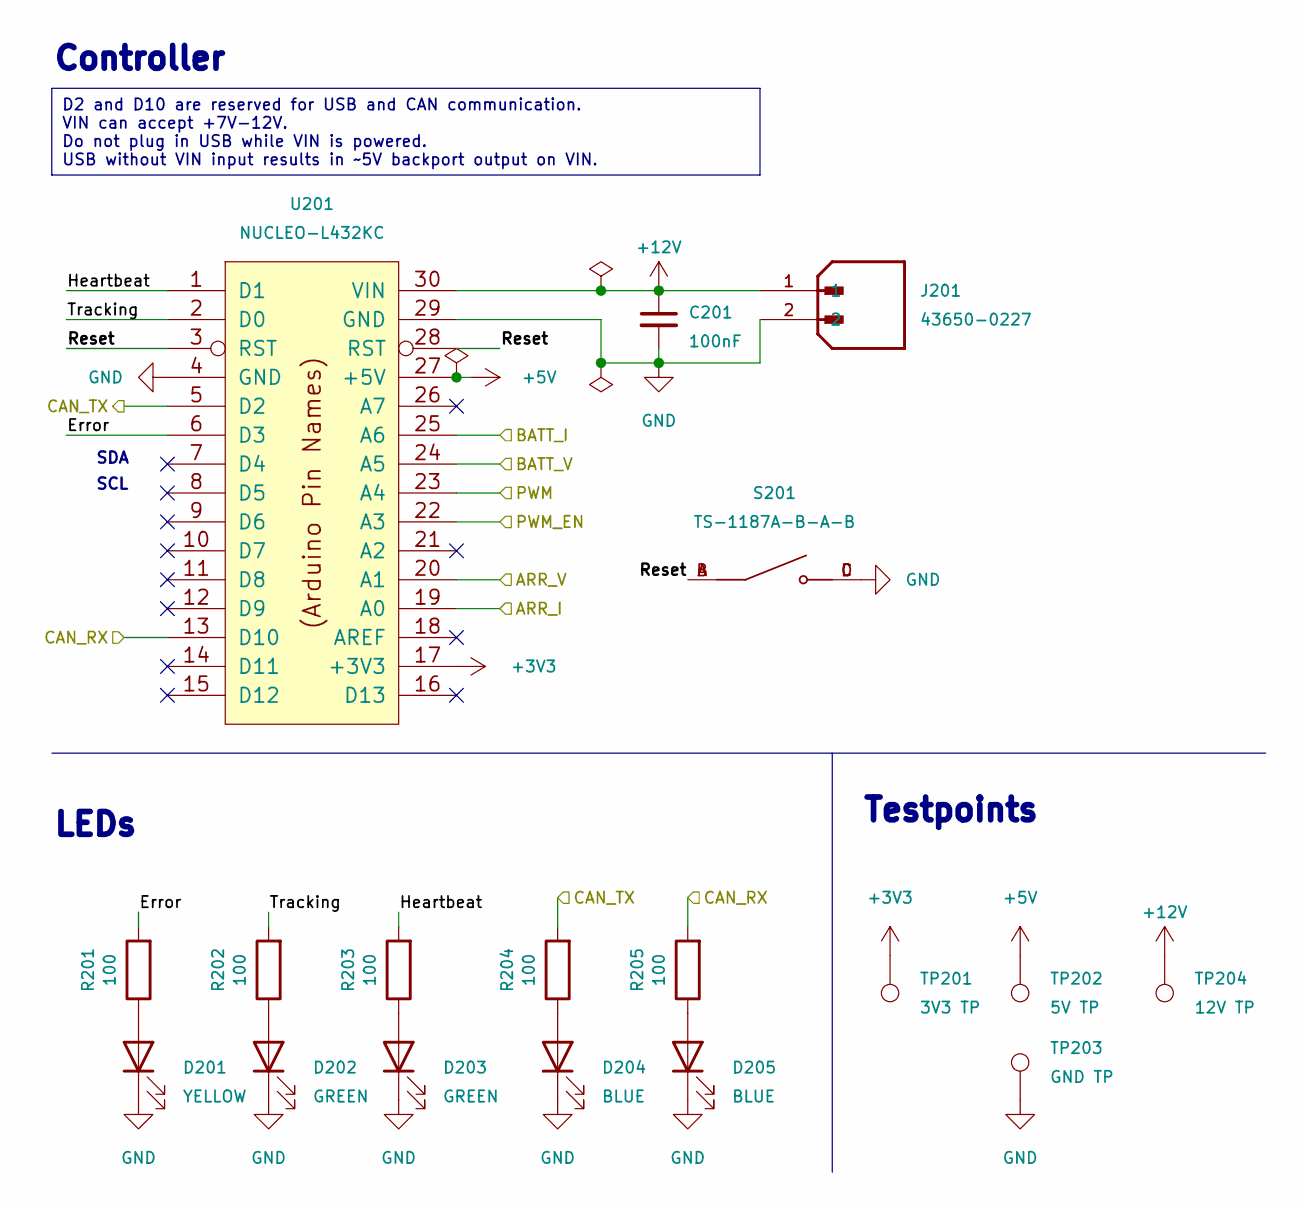
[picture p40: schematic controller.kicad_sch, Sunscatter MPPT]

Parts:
C201: 100nF; C_0402_1005Metric; LCSC Part # CL05B104KB54PNC
D201: YELLOW; LED_0603_1608Metric; LCSC Part # C72038
D202, D203: GREEN; LED_0603_1608Metric; LCSC Part # C72043
D204, D205: BLUE; LED_0603_1608Metric; LCSC Part # C72041
J201: 43650-0227; molex_microfit_43650_0227
R201, R202, R203, R204, R205: 100; R_0402_1005Metric; LCSC Part # C25076
S201: TS-1187A-B-A-B; xkb_TS_1187A_B_A_B; LCSC Part # C318884
TP201: 3V3 TP; TestPoint_Pad_1.0x1.0mm
TP202: 5V TP; TestPoint_Pad_1.0x1.0mm
TP203: GND TP; TestPoint_Pad_1.0x1.0mm
TP204: 12V TP; TestPoint_Pad_1.0x1.0mm
U201: NUCLEO-L432KC; stm_nucleo_L432KC

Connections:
+3V3: TP201.1, U201.17 (+3V3); also elsewhere on the board
/CAN_RX: R205.2, U201.13 (D10); also elsewhere on the board
/CAN_TX: R204.2, U201.5 (D2); also elsewhere on the board
/controller/ARR_I: U201.19 (A0); also elsewhere on the board
/controller/ARR_V: U201.20 (A1); also elsewhere on the board
/controller/BATT_I: U201.25 (A6); also elsewhere on the board
/controller/BATT_V: U201.24 (A5); also elsewhere on the board
/controller/Error: R201.2, U201.6 (D3)
/controller/Heartbeat: R203.2, U201.1 (D1)
/controller/PWM: U201.23 (A4); also elsewhere on the board
/controller/PWM_EN: U201.22 (A3); also elsewhere on the board
/controller/Reset: S201.A, S201.B, U201.3 (RST), U201.28 (RST)
/controller/Tracking: R202.2, U201.2 (D0)
GND: C201.2, D201.1 (K), D202.1 (K), D203.1 (K), D204.1 (K), D205.1 (K), J201.2, S201.C, S201.D, TP203.1, U201.4 (GND), U201.29 (GND); also elsewhere on the board
unnamed: D201.2 (A), R201.1
unnamed: D202.2 (A), R202.1
unnamed: D203.2 (A), R203.1
unnamed: D204.2 (A), R204.1
unnamed: D205.2 (A), R205.1

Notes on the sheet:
D2 and D10 are reserved for USB and CAN communication. VIN can accept +7V-12V. Do not plug in USB while VIN is powered. USB without VIN input results in ~5V backport output on VIN.
LEDs
SDA
Controller
Testpoints
SCL

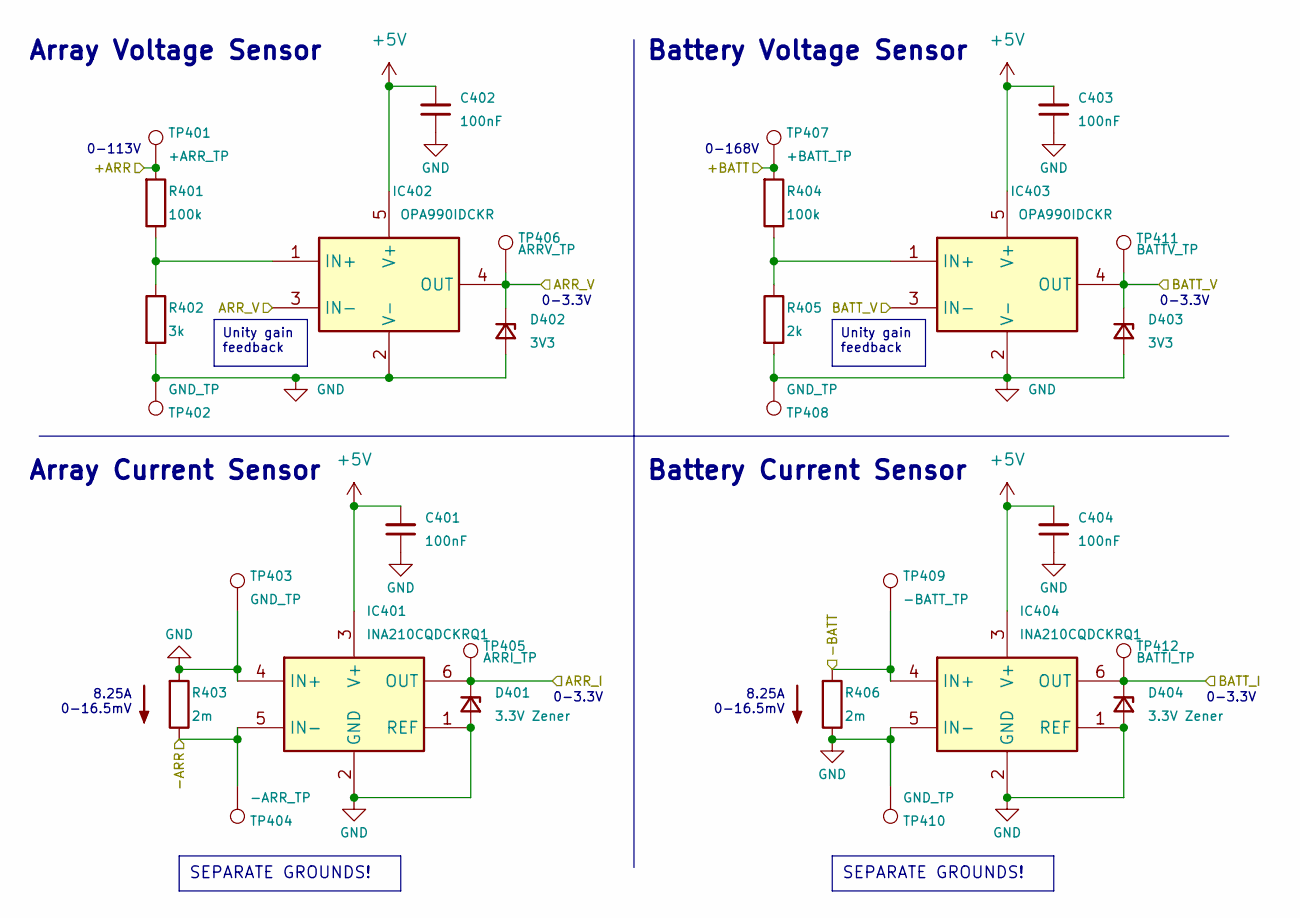
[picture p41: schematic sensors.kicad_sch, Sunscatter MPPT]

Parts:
C401, C402, C403, C404: 100nF; C_0402_1005Metric; LCSC Part # CL05B104KB54PNC
D401, D404: 3.3V Zener; D_MiniMELF; LCSC Part # C8056
D402, D403: 3V3; D_MiniMELF; LCSC Part # C8056
IC401, IC404: INA210CQDCKRQ1; ti_INA210CQDCKRQ1
IC402, IC403: OPA990IDCKR; ti_OPA990IDCKR
R401, R404: 100k; R_0805_2012Metric; LCSC Part # C149504
R402: 3k; R_0805_2012Metric; LCSC Part # C17661
R403, R406: 2m; R_1206_3216Metric
R405: 2k; R_0805_2012Metric; LCSC Part # C17604
TP401: +ARR_TP; TestPoint_Pad_1.0x1.0mm
TP402, TP403, TP408, TP410: GND_TP; TestPoint_Pad_1.0x1.0mm
TP404: -ARR_TP; TestPoint_Pad_1.0x1.0mm
TP405: ARRI_TP; TestPoint_Pad_1.0x1.0mm
TP406: ARRV_TP; TestPoint_Pad_1.0x1.0mm
TP407: +BATT_TP; TestPoint_Pad_1.0x1.0mm
TP409: -BATT_TP; TestPoint_Pad_1.0x1.0mm
TP411: BATTV_TP; TestPoint_Pad_1.0x1.0mm
TP412: BATTI_TP; TestPoint_Pad_1.0x1.0mm

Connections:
/V_ARR+: R401.2, TP401.1; also elsewhere on the board
/V_BATT+: R404.2, TP407.1; also elsewhere on the board
/controller/ARR_I: D401.1 (K), IC401.6 (OUT), TP405.1; also elsewhere on the board
/controller/ARR_V: D402.1 (K), IC402.3 (IN-), IC402.4 (OUT), TP406.1; also elsewhere on the board
/controller/BATT_I: D404.1 (K), IC404.6 (OUT), TP412.1; also elsewhere on the board
/controller/BATT_V: D403.1 (K), IC403.3 (IN-), IC403.4 (OUT), TP411.1; also elsewhere on the board
/converter/V_ARR-: IC401.5 (IN-), R403.1, TP404.1; also elsewhere on the board
/converter/V_BATT-: IC404.4 (IN+), R406.2, TP409.1; also elsewhere on the board
GND: C401.1, C402.1, C403.1, C404.1, D401.2 (A), D402.2 (A), D403.2 (A), D404.2 (A), IC401.1 (REF), IC401.2 (GND), IC401.4 (IN+), IC402.2 (V-), IC403.2 (V-), IC404.1 (REF), IC404.2 (GND), IC404.5 (IN-), R402.2, R403.2, R405.2, R406.1, TP402.1, TP403.1, TP408.1, TP410.1; also elsewhere on the board
unnamed: IC402.1 (IN+), R401.1, R402.1
unnamed: IC403.1 (IN+), R404.1, R405.1

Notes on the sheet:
SEPARATE GROUNDS!
Unity gain feedback
0-3.3V
Battery Voltage Sensor
0-113V
Battery Current Sensor
Array Current Sensor
Array Voltage Sensor
8.25A 0-16.5mV
0-168V

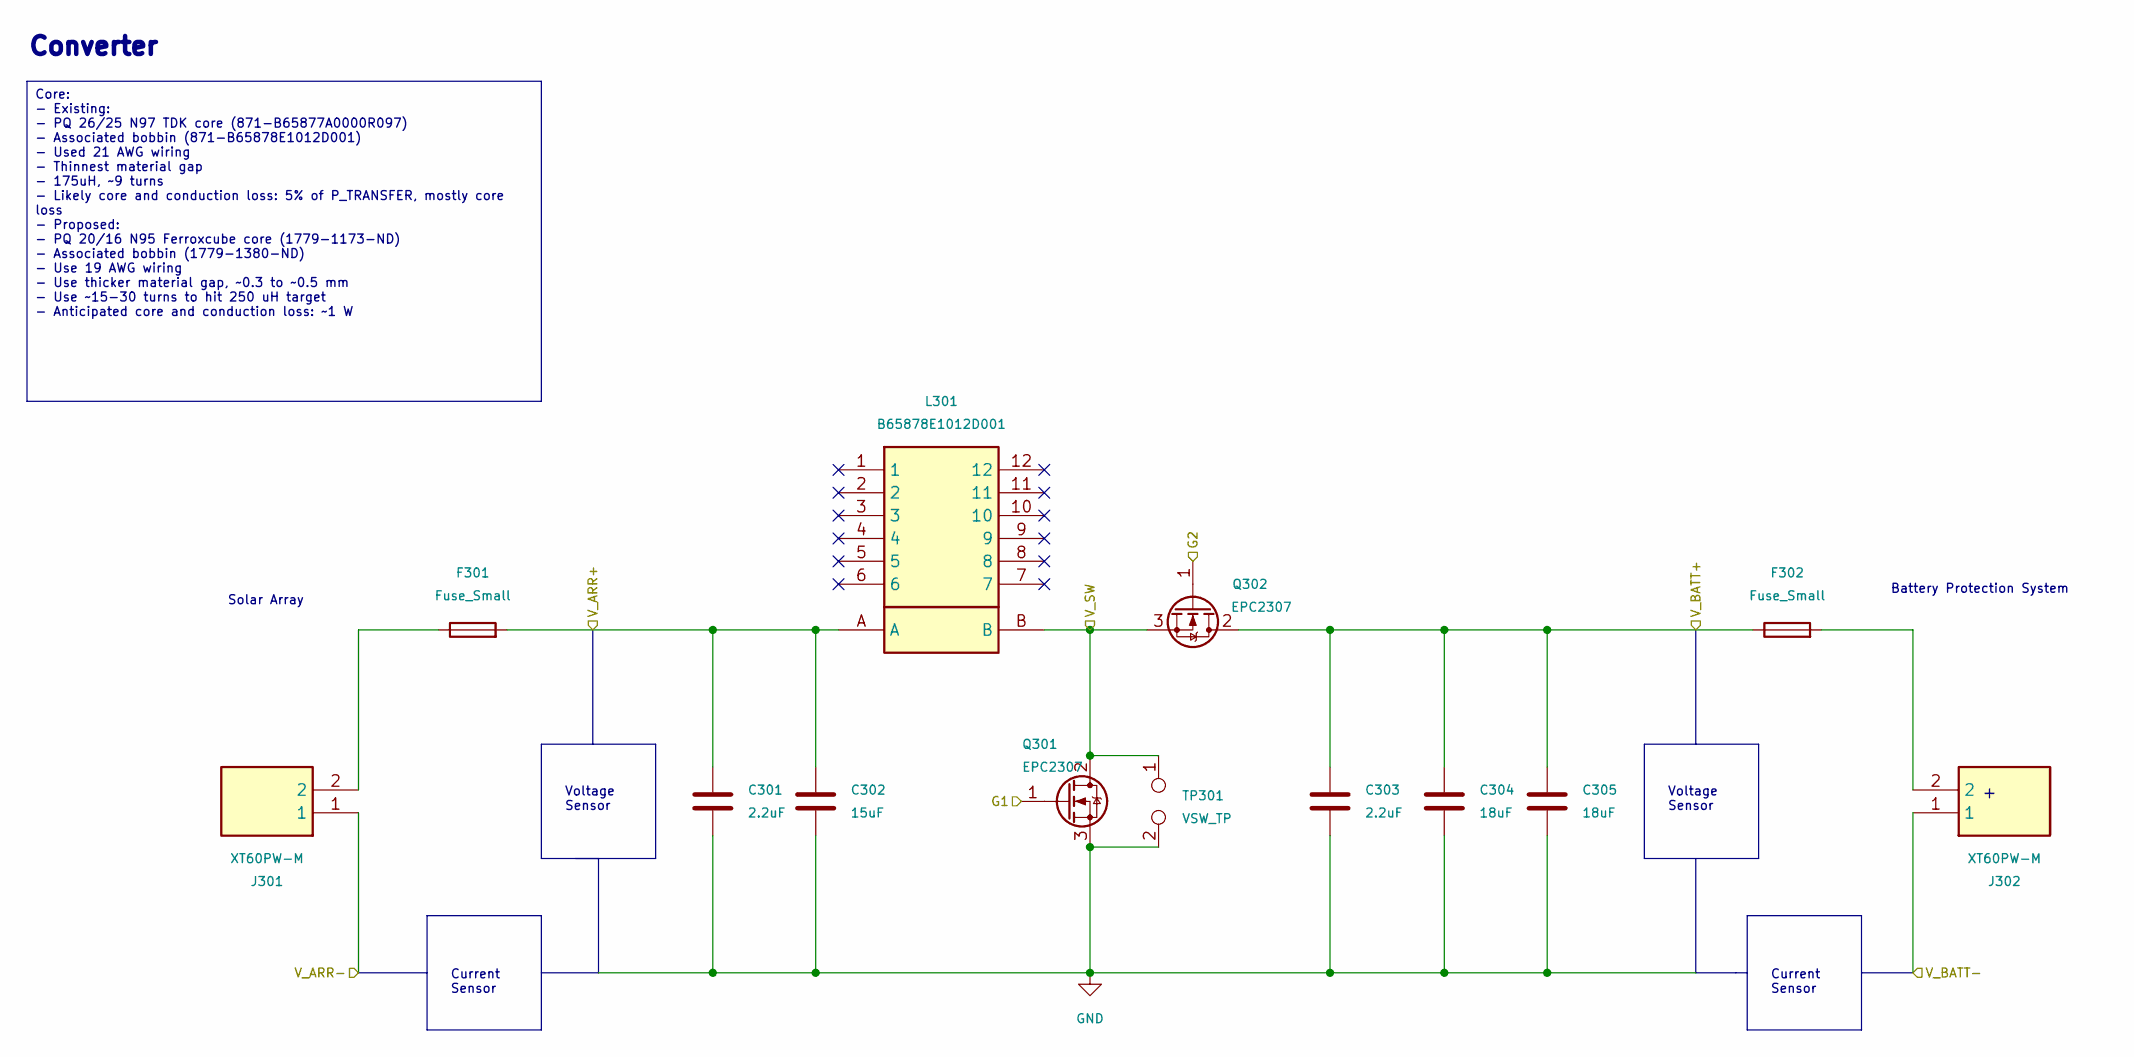
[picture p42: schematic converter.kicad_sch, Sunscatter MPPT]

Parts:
C301, C303: 2.2uF; C_2220_5650Metric
C302: 15uF; C_Radial_D8.0mm_H11.5mm_P3.50mm
C304, C305: 18uF; C_Radial_D10.0mm_H16.0mm_P5.00mm
F301, F302: Fuse_Small; littelfuse_05200101Z
J301, J302: XT60PW-M; AMASS_XT60PW-M_1x02_P7.20mm_Horizontal; LCSC Part # C98732
L301: B65878E1012D001; tdk_B65878E1012D001
Q301, Q302: EPC2307; epc_EPC2307
TP301: VSW_TP; TestPoint_2Pads_Pitch5.08mm_Drill1.3mm

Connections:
/V_ARR+: C301.1, C302.1, F301.2, L301.A; also elsewhere on the board
/V_BATT+: C303.1, C304.1, C305.1, F302.1, Q302.2 (D); also elsewhere on the board
/V_SW: L301.B, Q301.2 (D), Q302.3 (S), TP301.1; also elsewhere on the board
/converter/G1: Q301.1 (G); also elsewhere on the board
/converter/G2: Q302.1 (G); also elsewhere on the board
/converter/V_ARR-: J301.1; also elsewhere on the board
/converter/V_BATT-: J302.1; also elsewhere on the board
GND: C301.2, C302.2, C303.2, C304.2, C305.2, Q301.3 (S), TP301.2; also elsewhere on the board
unnamed: F301.1, J301.2
unnamed: F302.2, J302.2

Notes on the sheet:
Core: - Existing: - PQ 26/25 N97 TDK core (871-B65877A0000R097) - Associated bobbin (871-B65878E1012D001) - Used 21 AWG wiring - Thinnest material gap - 175uH, ~9 turns - Likely core and conduction loss: 5% of P_TRANSFER, mostly core loss - Proposed: - PQ 20/16 N95 Ferroxcube core (1779-1173-ND) - 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
Converter
Battery Protection System
Voltage Sensor
Current Sensor
Solar Array

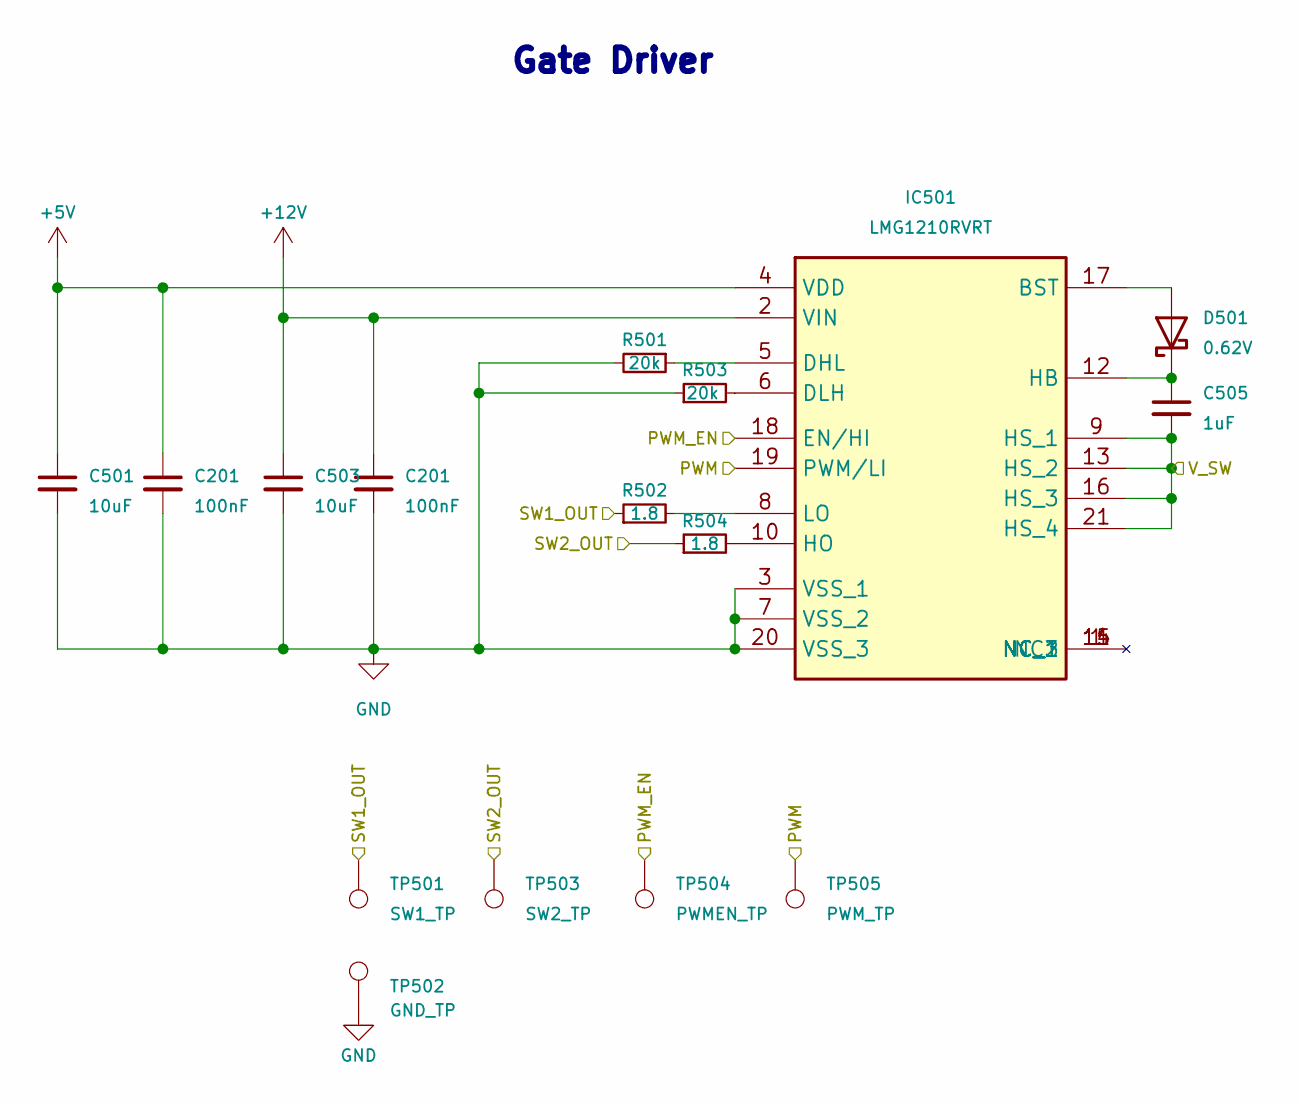
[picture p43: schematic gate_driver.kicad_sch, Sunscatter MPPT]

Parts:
C201: 100nF; C_0402_1005Metric; LCSC Part # CL05B104KB54PNC
C501, C503: 10uF; C_0603_1608Metric; LCSC Part # C96446
C505: 1uF; C_0402_1005Metric; LCSC Part # C52923
D501: 0.62V; stm_STPS1170AF
IC501: LMG1210RVRT; ti_LMG1210RVRT
R501, R503: 20k; R_0402_1005Metric; LCSC Part # C25765
R502, R504: 1.8; R_0402_1005Metric; LCSC Part # C423254
TP501: SW1_TP; TestPoint_Keystone_5005-5009_Compact
TP502: GND_TP; TestPoint_Keystone_5005-5009_Compact
TP503: SW2_TP; TestPoint_Keystone_5005-5009_Compact
TP504: PWMEN_TP; TestPoint_Pad_1.0x1.0mm
TP505: PWM_TP; TestPoint_Pad_1.0x1.0mm

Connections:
/V_SW: C505.2, IC501.9 (HS_1), IC501.13 (HS_2), IC501.16 (HS_3), IC501.21 (HS_4); also elsewhere on the board
/controller/PWM: IC501.19 (PWM/LI), TP505.1; also elsewhere on the board
/controller/PWM_EN: IC501.18 (EN/HI), TP504.1; also elsewhere on the board
/converter/G1: R502.1, TP501.1; also elsewhere on the board
/converter/G2: R504.1, TP503.1; also elsewhere on the board
GND: C201.2, C501.2, C503.2, IC501.3 (VSS_1), IC501.7 (VSS_2), IC501.20 (VSS_3), R501.2, R503.1, TP502.1; also elsewhere on the board
unnamed: D501.2 (A), IC501.17 (BST)
unnamed: C505.1, D501.1 (K), IC501.12 (HB)
unnamed: IC501.5 (DHL), R501.1
unnamed: IC501.6 (DLH), R503.2
unnamed: IC501.10 (HO), R504.2
unnamed: IC501.8 (LO), R502.2

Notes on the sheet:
Gate Driver

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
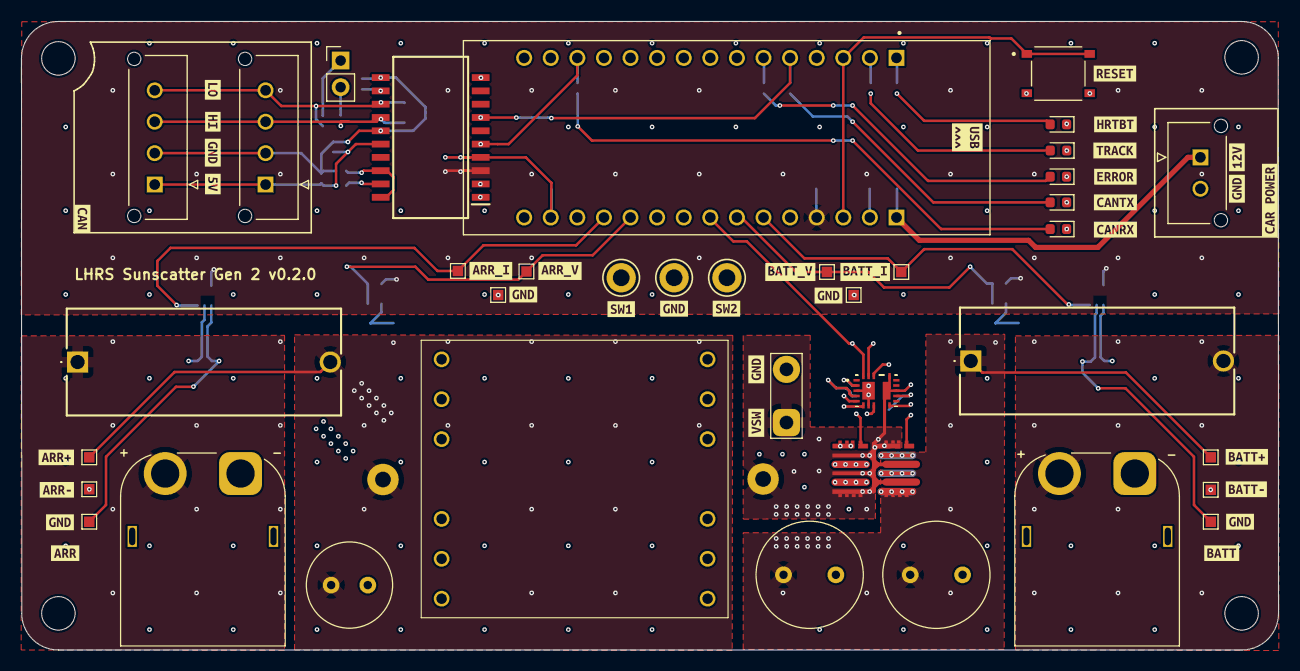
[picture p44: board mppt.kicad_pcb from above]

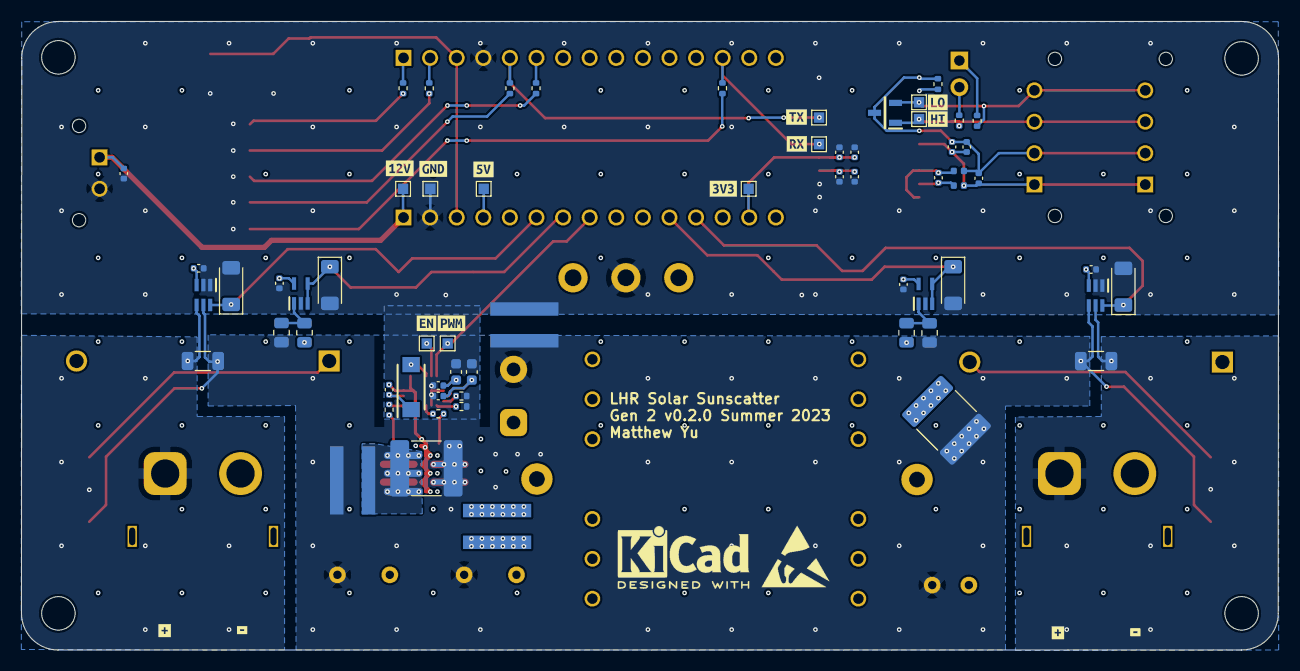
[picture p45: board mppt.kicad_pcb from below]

Board: 4 copper layers, 120.1 x 60.0 mm, 154 parts (77 on the bottom side), 47 nets.

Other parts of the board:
C502, C504: 100nF; C_0402_1005Metric
TJ101, TJ102, TJ103: Thermal Jumper; vishay_THJP1225ABT1
kibuzzard-64BB95E9: G***; kibuzzard-64BB95E9
kibuzzard-64BB97BE: G***; kibuzzard-64BB97BE
kibuzzard-64BB97CA: G***; kibuzzard-64BB97CA
kibuzzard-64BB97F0, kibuzzard-64BB97F0#2: G***; kibuzzard-64BB97F0
kibuzzard-64BB97FE, kibuzzard-64BB97FE#2: G***; kibuzzard-64BB97FE
kibuzzard-64BB98F2: G***; kibuzzard-64BB98F2
kibuzzard-64BB98F8: G***; kibuzzard-64BB98F8
kibuzzard-64BB954F: G***; kibuzzard-64BB954F
kibuzzard-64BB964A: G***; kibuzzard-64BB964A
kibuzzard-64BB966B: G***; kibuzzard-64BB966B
kibuzzard-64BB968B: G***; kibuzzard-64BB968B
kibuzzard-64BB971E: G***; kibuzzard-64BB971E
kibuzzard-64BB973A: G***; kibuzzard-64BB973A
kibuzzard-64BB974F: G***; kibuzzard-64BB974F
kibuzzard-64BB975A: G***; kibuzzard-64BB975A
kibuzzard-64BB994C: G***; kibuzzard-64BB994C
kibuzzard-64BB9525: G***; kibuzzard-64BB9525
kibuzzard-64BB9530: G***; kibuzzard-64BB9530
kibuzzard-64BB9539: G***; kibuzzard-64BB9539
kibuzzard-64BB9548: G***; kibuzzard-64BB9548
kibuzzard-64BB9585: G***; kibuzzard-64BB9585
kibuzzard-64BB9776: G***; kibuzzard-64BB9776
kibuzzard-64BB9873, kibuzzard-64BB9873#2: G***; kibuzzard-64BB9873
kibuzzard-64BB9946: G***; kibuzzard-64BB9946
kibuzzard-64BBA6A3: G***; kibuzzard-64BBA6A3
kibuzzard-64BBA6B0, kibuzzard-64BBA6B0#2: G***; kibuzzard-64BBA6B0
kibuzzard-64BBA8A0: G***; kibuzzard-64BBA8A0
kibuzzard-64BBA8B2: G***; kibuzzard-64BBA8B2
kibuzzard-64BBA8C3: G***; kibuzzard-64BBA8C3
kibuzzard-64BBA8E6: G***; kibuzzard-64BBA8E6
kibuzzard-64BBA9B6: G***; kibuzzard-64BBA9B6
kibuzzard-64BBA9C0: G***; kibuzzard-64BBA9C0
kibuzzard-64BBA9D4: G***; kibuzzard-64BBA9D4
kibuzzard-64BBA88C: G***; kibuzzard-64BBA88C
kibuzzard-64BBA694: G***; kibuzzard-64BBA694
kibuzzard-64BBA752: G***; kibuzzard-64BBA752
kibuzzard-64BBA758: G***; kibuzzard-64BBA758
kibuzzard-64BBA896: G***; kibuzzard-64BBA896
kibuzzard-64BBAA49: G***; kibuzzard-64BBAA49
kibuzzard-64BBAA54: G***; kibuzzard-64BBAA54
kibuzzard-64BC07CB: G***; kibuzzard-64BC07CB
kibuzzard-64BC07D4: G***; kibuzzard-64BC07D4
kibuzzard-64BC07E0: G***; kibuzzard-64BC07E0
kibuzzard-64BC07EC: G***; kibuzzard-64BC07EC

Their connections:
/V_BATT+: TJ101.2 (B), TJ102.2 (B); also elsewhere on the board
/V_SW: TJ101.1 (A); also elsewhere on the board
GND: C502.2, C504.2, TJ102.1 (A), TJ103.1 (A), TJ103.2 (B); also elsewhere on the board

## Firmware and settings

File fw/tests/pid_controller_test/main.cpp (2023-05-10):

/**
 * @file main.cpp
 * @author Matthew Yu (matthewjkyu@gmail.com)
 * @brief Performs basic PID controller loop for fixed output given some input
 *        lower than the output.
 * @version 0.1
 * @date 2023-04-02
 * @note For board revision v0.1.0.
 * @copyright Copyright (c) 2023
 *
 */

#include <math.h>
#include "mbed.h"
#include "FastPWM.h"
#include "./pid_controller/pid_controller.hpp"
#include "./Filter/SmaFilter.h"

#define F_SW 104000.0 // 104 khz switching
#define TARGET 86.0

// Note: only read AnalogIn in one ISR ever since we aren't using mutexes.
class UnlockedAnalogIn : public AnalogIn {
public:
    UnlockedAnalogIn(PinName inp) : AnalogIn(inp) { }
    virtual void lock() { }
    virtual void unlock() { }
};

typedef enum Error { 
    OK=0,
    INP_UVL=100,
    INP_OVL=101,
    OUT_UVL=102,
    OUT_OVL=103,
    INP_OUT_INV=104,
} ErrorCode;
ErrorCode status = OK;

PIDConfig_t pidConfig = PIDControllerInit(0.9, -0.9, 5E-4, 3E-6, 0.0);

DigitalOut led_heartbeat(PA_9);
DigitalOut led_tracking(PA_10);
DigitalOut led_error(PA_12);
DigitalOut pwm_enable(PA_3);
FastPWM pwm_out(PA_1);
UnlockedAnalogIn arr_voltage_sensor(PA_4);
UnlockedAnalogIn arr_current_sensor(PA_5);
UnlockedAnalogIn batt_voltage_sensor(PA_7);
UnlockedAnalogIn batt_current_sensor(PA_6);
SmaFilter arr_voltage_filter(1);
SmaFilter batt_voltage_filter(1);
SmaFilter arr_current_filter(1);
SmaFilter batt_current_filter(1);

Ticker ticker_toggle_heartbeat;
Ticker ticker_read_sensor;
Ticker ticker_update_pwm;
Ticker ticker_check_redlines;

static int x = 0;

float calibrate_arr_v(float inp) {
    if (inp < 1.0) return inp * 114.0;
    else return 114.0;
}

float calibrate_arr_i(float inp) {
    if (inp < 1.0) return inp * 5.79 + 0.0042;
    else return 5.79;
}

float calibrate_batt_v(float inp) {
    if (inp < 1.0) return inp * 168.0 + 0.0393;
    else return 168.0;
}

float calibrate_batt_i(float inp) {
    if (inp < 1.0) return inp * 5.8 + 0.0167;
    else return 5.8;
}

void heartbeat() { led_heartbeat = !led_heartbeat; }

void read_sensor(void) {
    float arr_v = calibrate_arr_v(arr_voltage_sensor.read());
    float arr_i = calibrate_arr_i(arr_current_sensor.read());
    float batt_v = calibrate_batt_v(batt_voltage_sensor.read());
    float batt_i = calibrate_batt_i(batt_current_sensor.read());

    // INJECT NOISE :O
    float amplitude = TARGET * 0.001;
    float noise = sin(3.14/100 * (++x)) * amplitude;
    batt_v += noise;

    arr_voltage_filter.addSample(arr_v);
    arr_current_filter.addSample(arr_i);
    batt_voltage_filter.addSample(batt_v);
    batt_current_filter.addSample(batt_i);
}
void run_pid_controller(void) {
    // Duty direction is reverse of error, so we invert the result.
    float change = PIDControllerStep(pidConfig, (double) TARGET, (double) batt_voltage_filter.getResult());
    float duty = pwm_out.read();
    float new_duty = duty - change;
    if (new_duty > 0.90) {
        duty = 0.90;
    } else if (new_duty < 0.10) {
        duty = 0.10;
    } else {
        duty = new_duty;
    }

    pwm_out.write(duty);
}
void _assert(bool condition, ErrorCode code) {
    // If we fail our condition, raise the flag and let the main thread handle it.
    if (!condition) { status = code; }
}
void check_redlines(void) {
    float arr_v_filtered = arr_voltage_filter.getResult();
    float batt_v_filtered = batt_voltage_filter.getResult();

    // Our input must be in the range (1.0, 80.0).
    _assert(arr_v_filtered > 1.0, INP_UVL);
    _assert(arr_v_filtered < 70.0, INP_OVL);

    // Our output must be between (80.0, 130.0).
    _assert(batt_v_filtered > 70.0, OUT_UVL);
    _assert(batt_v_filtered < 130.0, OUT_OVL);

    // Our output must always be greater than our input.
    _assert(arr_v_filtered < batt_v_filtered, INP_OUT_INV);
}

#define CYCLE_PERIOD 5ms
int main()
{
    set_time(1680461674);
    
    printf("Hello world. PID Controller example. starting up.\n");
    
    // Start heartbeat.
    ticker_toggle_heartbeat.attach(&heartbeat, 1000ms);
    ticker_read_sensor.attach(&read_sensor, CYCLE_PERIOD);

    // 5 seconds for user to get ready.
    ThisThread::sleep_for(5000ms);

    // Set the pwm frequency to 104 kHz.
    pwm_out.period_us(1.0E6 / F_SW);
    pwm_out.write(0.10); // Default duty cycle of 50%.

    // Start tracking.
    led_tracking = 1;
    pwm_enable = 1;

    ThisThread::sleep_for(500ms);
    ticker_check_redlines.attach(&check_redlines, 10ms);

    // Start pwm update.
    ticker_update_pwm.attach(&run_pid_controller, CYCLE_PERIOD);
    while (true) {
        ThisThread::sleep_for(CYCLE_PERIOD);
        // CSV format for later analysis.
        float amplitude = TARGET * 0.001;
        float noise = sin(3.14/100 * (x)) * amplitude;
        printf(
            "%u, %f, %f, %f, %f, %f, %f\n", 
            time(NULL), 
            arr_voltage_filter.getResult(),
            arr_current_filter.getResult(),
            batt_voltage_filter.getResult(),
            batt_current_filter.getResult(),
            pwm_out.read(),
            noise
        );

        if (status != OK) {
            pwm_enable = 0;
            led_tracking = 0;
            printf("A redline (%u) has been crossed. Tracking is disabled.\n", status);
            while (true) {
                ThisThread::sleep_for(1000ms);
            }
        }
    }
}

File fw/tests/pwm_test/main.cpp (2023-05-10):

/**
 * @file main.cpp
 * @author Matthew Yu (matthewjkyu@gmail.com.com)
 * @brief Tests the PWM gate driver. Two modes, one for feedback using BNC, the
 *        other uses manual control.
 * @version 0.1
 * @date 2023-03-26
 * @note For board revision v0.1.0. To load FastPWM: import http://os.mbed.com/users/Sissors/code/FastPWM/
 * @copyright Copyright (c) 2023
 *
 */

#include "mbed.h"
#include "FastPWM.h"
#include <chrono>
using namespace std::chrono;


// Switching frequency is 104kHz.
// Duty cycle is a function of pwm_control, which takes a value from 0 - 1 V.


#define __MODE__ 0 // 0 for using BNC, 1 if manual control

#if __MODE__ == 0
class UnlockedAnalogIn : public AnalogIn {
public:
    UnlockedAnalogIn(PinName inp) : AnalogIn(inp) { }
    virtual void lock() { }
    virtual void unlock() { }
};

DigitalOut led_heartbeat(PA_9);
DigitalOut led_tracking(PA_10);
DigitalOut pwm_enable(PA_3);
UnlockedAnalogIn pwm_control(PA_0);
FastPWM pwm_out(PA_1);

Ticker ticker_heartbeat;
Timer t;


void heartbeat() { led_heartbeat = !led_heartbeat; }
inline void adjust_duty_cycle() {
    pwm_out.write(pwm_control.read());
}

int main()
{
    // Set the pwm frequency to 104 kHz.
    float f = 100000.0;
    pwm_out.period_us(1.0E6 / f);
 
    // Indicate that pwm is running.
    led_tracking = 1;

    // Start heartbeat.
    ticker_heartbeat.attach(&heartbeat, 1000ms);

    printf("HELLO WORLD MOKUGO MODE\n");
    // Start PWM control.
    pwm_enable = 1;

    while (true) {
        // 22 uS, max update freq is ~45kHz
        // uint32_t i;
        // t.reset();
        // t.start();
        // for (i = 0; ++i < 100000;) {
            adjust_duty_cycle();
        // }
        // t.stop();
        // printf("The time taken was %llu microseconds\n", duration_cast<microseconds>(t.elapsed_time()/100000).count());
    }
}


#else

DigitalOut led_heartbeat(PA_9);
DigitalOut led_tracking(PA_10);
DigitalOut pwm_enable(PA_3);
FastPWM pwm_out(PA_1);

Ticker ticker_heartbeat;
Ticker ticker_pwm_update;

void heartbeat() { led_heartbeat = !led_heartbeat; }
void adjust_duty_cycle() {
    static int inp = 0.0;
    static float n = 1;
    inp = (inp + 1) % 101;
    pwm_out.write((float) inp / 100.00);
}

int main()
{
    // Set the pwm frequency to 104 kHz.
    printf("HELLO WORLD FIXED MODE\n");
    float f = 100000.0;
    float d = 1-0.5;
    pwm_out.period_us(1.0E6 / f);
    pwm_out.write(d);

    // Indicate that pwm is running.
    led_tracking = 1;

    // Start heartbeat.
    ticker_heartbeat.attach(&heartbeat, 500ms);

    // Start PWM control.
    pwm_enable = 1;
    // ticker_pwm_update.attach(&adjust_duty_cycle, 100ms);

    while (true) {
        ThisThread::sleep_for(1000ms);
    }
}

#endif

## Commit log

2023-01-31 init commit
    [controller.kicad_sch, converter.kicad_sch, gate_driver.kicad_sch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]
2023-02-02 initial sim files for kicad spice sim, freeze on design.py
    [MOSFET_SELECTION.ods, MOSFET_SELECTION.xlsx, mppt-spice-sim.kicad_pcb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]
2023-02-03 fix bugs and standard inputs/output
    [MOSFET_SELECTION.xlsx]
2023-02-03 save comments for mosfet selection
    [MOSFET_SELECTION.xlsx]
2023-02-03 TODO for change
    [MOSFET_SELECTION.xlsx]
2023-02-07 commit last run of sw
    [mppt-spice-sim.kicad_sch]
2023-02-26 working on documentation, design methmethodology, sizing, layout
    [1935776.step, Untitled 1.ods, controller.kicad_sch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]
2023-02-26 parts of gate driver
    [controller.kicad_sch, converter.kicad_sch, gate_driver.kicad_sch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]
2023-02-27 laid out MOSFET switching loop and thermal connections
    [converter.kicad_sch, gate_driver.kicad_sch, mppt.kicad_pcb]
2023-02-27 made gate driver loop v1
    [converter.kicad_sch, gate_driver.kicad_sch, mppt.kicad_pcb]
2023-02-27 layout revision this one is cursed
    [controller.kicad_sch, converter.kicad_sch, gate_driver.kicad_sch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]
2023-02-27 slight bom updates
    [controller.kicad_sch, gate_driver.kicad_sch, sensors.kicad_sch]
2023-02-27 improved thermals of fets with internal vias, internal traces, and thermal jumpers
    [converter.kicad_sch, mppt.kicad_pcb]
2023-02-28 even better thermal design, kept pours out of MOSFET pins and sswitched to 0805 thermal jumpers
    [converter.kicad_sch, mppt.kicad_pcb]
2023-02-28 revision of PCB layout
    [controller.kicad_sch, converter.kicad_sch, gate_driver.kicad_sch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]
2023-03-02 segregating code into design procedures
    [Untitled 1.ods, controller.kicad_sch, converter.kicad_sch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]
2023-03-03 Design partioning, might've gotten the parameters down, more documents
    [MOSFET_SELECTION.ods, MOSFET_SELECTION.xlsx, converter.kicad_sch]
2023-03-04 added Vsw test point and altered Vsw trace slightly
    [converter.kicad_sch, mppt.kicad_sch]
2023-03-04 Added proper signal TPs for Vsw, both gate signals, and PWM, added BNC connector for PWM control signal to STM analog pin, increased Vsw zone on F.cu, in.1, and in.2, reduced vias directly under fets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
    [controller.kicad_sch, converter.kicad_sch, gate_driver.kicad_sch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]
2023-03-05 changed low-speed test points to through-hole standoffs, created a thermal sink area for high-side fet on B.Cu, and changed some thermal resistors to larger 1225 package where available due to lower 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
    [controller.kicad_sch, mppt.kicad_sch, sensors.kicad_sch]
2023-03-06 rebuild schematic, passes ERC, bom completed
    [B32524R3156M000.stp, B65878E1012D001.stp, OPA990IDCKR.stp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]
2023-03-06 screw locks
2023-03-06 savestate layout
    [controller.kicad_sch, converter.kicad_sch, gate_driver.kicad_sch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]
2023-03-06 final layout
    [converter.kicad_sch, mppt.kicad_pcb, mppt.kicad_sch]
2023-03-06 temp for matthew to stitch
    [converter.kicad_sch, mppt.kicad_pcb, mppt.kicad_sch]
2023-03-08 production files for v0.1.0. Change cap power calc to be based off i_rms of i_pkpk, not i_pk + r_l_a
    [controller.kicad_sch, converter.kicad_sch, gate_driver.kicad_sch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]
2023-03-09 update bom
2023-03-09 added TJ's and 15uF output capacitor population options
    [converter.kicad_sch, mppt.kicad_sch]
2023-03-10 fixed gate driver circuit, filleted filled zones, ensured DRC conformity regarding clearances
    [controller.kicad_sch, gate_driver.kicad_sch]
2023-03-26 writing fw tests
    [converter.kicad_sch, gate_driver.kicad_sch]
2023-04-02 fixes for v0.1.1rc
    [controller.kicad_sch, converter.kicad_sch, gate_driver.kicad_sch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]
2023-04-02 updated pid controller test with changes from boost test, we have experienced convergence :eyes:
2023-04-02 note that indicator LED pins should hook up to PWM in v0.1.1rc for dimming
    [mppt.kicad_sch]
2023-04-21 updated instructions for v0.2.0 - v0.5.0 development candidates.
    [controller.kicad_sch, converter.kicad_sch, gate_driver.kicad_sch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]
2023-05-10 v0.2.0 design automation, documentation
    [FXCStainmetzCoefficients.xls, MOSFET_SELECTION.ods, MOSFET_SELECTION.xlsx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]
2023-06-26 hw changes
    [1935776.step, B32524R3156M000.stp, B65878E1012D001.stp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]
2023-07-17 rm dev folder which breaks linux kids
    [Untitled 1.ods]
2023-07-22 bugfix for wrong adc pin for batt current measurements
    [comm_can.kicad_sch, controller.kicad_sch, converter.kicad_sch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]
2023-07-27 savestate, remove extraneous files
    [mppt.ods]
2023-08-12 fix for swapped xt60 connectors
    [converter.kicad_sch, mppt.kicad_pcb]
